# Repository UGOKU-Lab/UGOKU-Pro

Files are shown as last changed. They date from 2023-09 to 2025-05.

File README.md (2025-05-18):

# UGOKU One
UGOKU Pro のハードウェア設計データ（KiCADデータ）のリポジトリです。

UGOKU Pro はモータやセンサを使ったロボットなどのアプリケーションを少しでも手軽にテスト、制御することを目的に開発している汎用基板です。

広く普及しているマイコンボードや無線モジュールに加え、高出力なDCモータドライバを2個搭載しています。さらに、汎用IOポートを設け幅広いアプリケーションに対応します。
Androidアプリ[FlexConsole](https://github.com/UGOKU-Lab/FlexConsole_for_Bluetooth_Serial)と組み合わせることでスマートフォンから手軽に遠隔操作や監視が行えます。

[](

)

| 主要搭載部品 |  |
----|---- 
| マイコンボード | Nucleo-F303K8 | 
| 無線モジュール | ESP32-WROOM-32E |
| DCモータドライバ | 2× TB67H303HG |
| CANトランシーバ | MCP2562-E/SN |

# 使用ライブラリ
[SnapMagic](https://www.snapeda.com/home/) よりダウンロードしたKiCADのライブラリ（CC BY-SA）を使用しています

# ライセンス
<br />この データ は <a rel="license" href="http://creativecommons.org/licenses/by-sa/4.0/deed.ja">クリエイティブ・コモンズ 表示 4.0 国際 ライセンス</a>の下に提供されています。

本データおよび本データにより製作した基板は良識の範囲で自由に非営利、営利問わず使用できます。また、改変、再配布も可能です。
ただし、再配布の際には本リポジトリのリンクを掲載を希望します。（本プロジェクトの目的に即した改良についてはプルリクエストを歓迎します）。  
また、本データにより生じた損害等の一切の責任を負いかねますので、ご了承ください。

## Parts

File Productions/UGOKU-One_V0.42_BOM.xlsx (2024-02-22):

Comment | Designator | Footprint | JLCPCB Part #（optional）
100nF | C1, C11, C13, C2, C3, C4, C9 | C0805 | C1711
3.3uF | C10 | C0805 | C2182175
51k | R13, R7 | R0603
10k | R2, R3, R12, R9 | R0603
120 | R1 | R0603
510 | R4 | R0603 | C965132
1k | R5, R6 | R0603
LED | L1 | L0805 | C264427
LED | L2, L3 | L0805 | C86865
Diode | D1 | SOD-123F
SSSS213202 | SW3, SW5 |  | C115375
TL3301FF160QG | SW1, SW2 |  | C273522
SKRPABE010 | SW4 |  | C115360
MCP2562-E/SN | U6 | SOIC127P600X175-8N | C53609
ESP32-WROOM-32E-N16 | U7 |  | C701343
TB67H303HG | U4,U5 |  | C1556864
1792863 | T1,T2,T3 |  | C3032345
A2541WV-3P | J4 |  | C5333416
B03B-XASK-1-A(LF)(SN) | CN4 |  | C264992
B04B-XASK-1(LF)(SN) | CN1,CN2,CN3 |  | C264994
A2541HWV-4P | J6 |  | C5176037
PZ254V-12-6P | J1 |  | C492420
B-2200S15P-A120 | P1,P2 |  | C124408

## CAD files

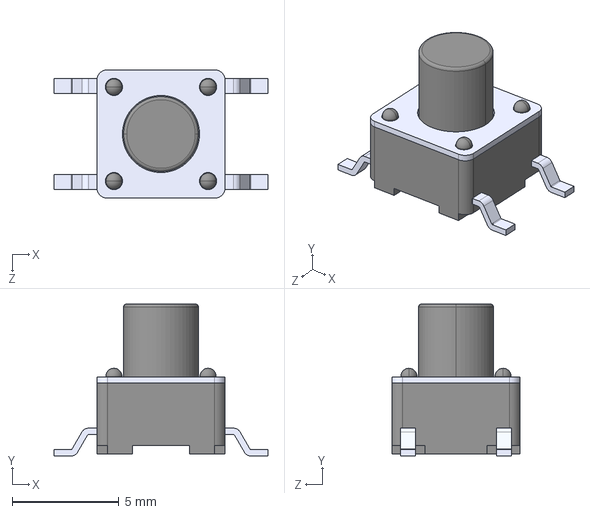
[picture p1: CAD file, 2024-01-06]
3Dmodels/TL3301FF160QG.step
10.0 x 7.10 x 6.00 mm

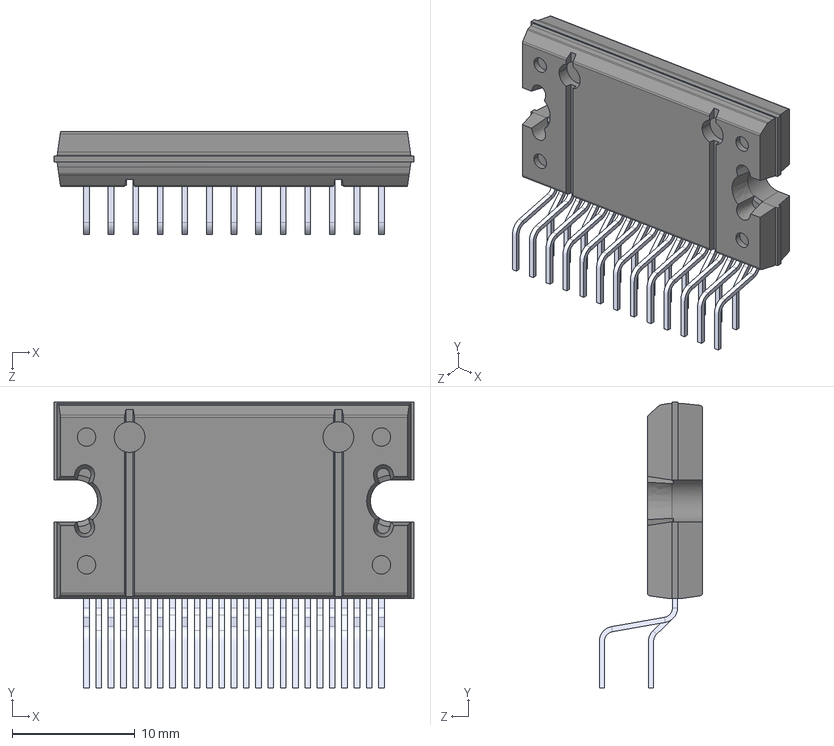
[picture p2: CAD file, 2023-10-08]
3Dmodels/TB67H303HG.step
29.3 x 23.3 x 8.41 mm

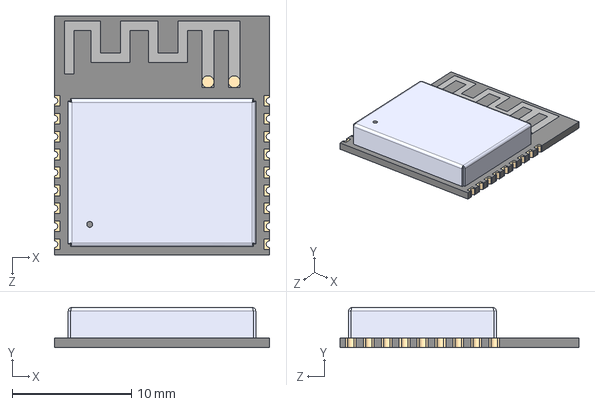
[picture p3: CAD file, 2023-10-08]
3Dmodels/ESP32-C3-WROOM-02-N4.step
18.0 x 3.35 x 20.0 mm

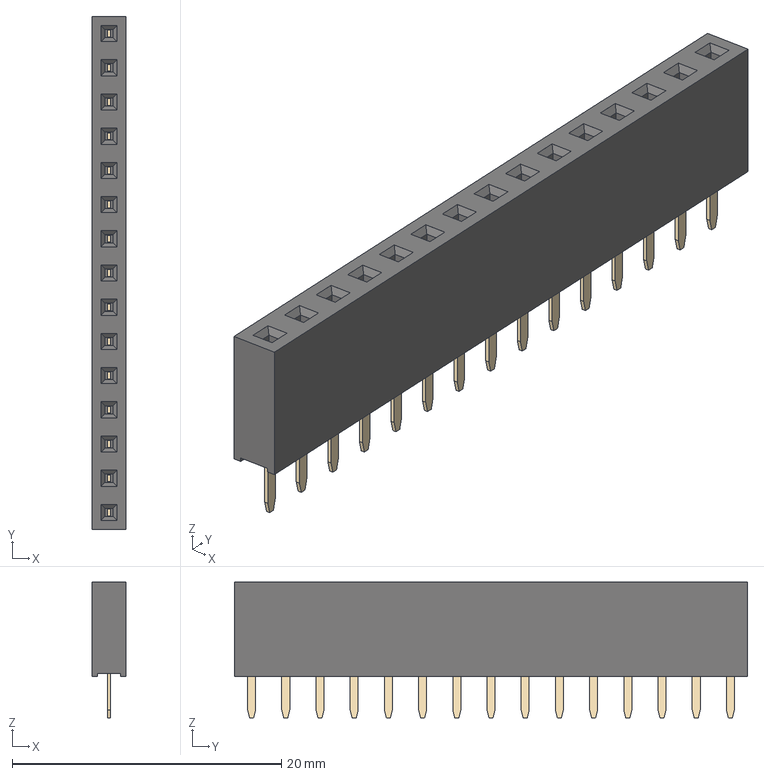
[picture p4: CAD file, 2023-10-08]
3Dmodels/PinSocket_1x15_P2.54mm_Vertical.step
2.54 x 38.1 x 10.1 mm

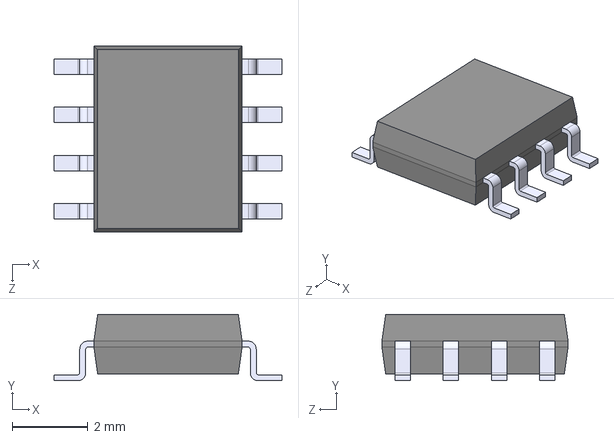
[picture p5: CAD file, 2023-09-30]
3Dmodels/MCP2562-E_SN.step
6.00 x 1.75 x 4.90 mm

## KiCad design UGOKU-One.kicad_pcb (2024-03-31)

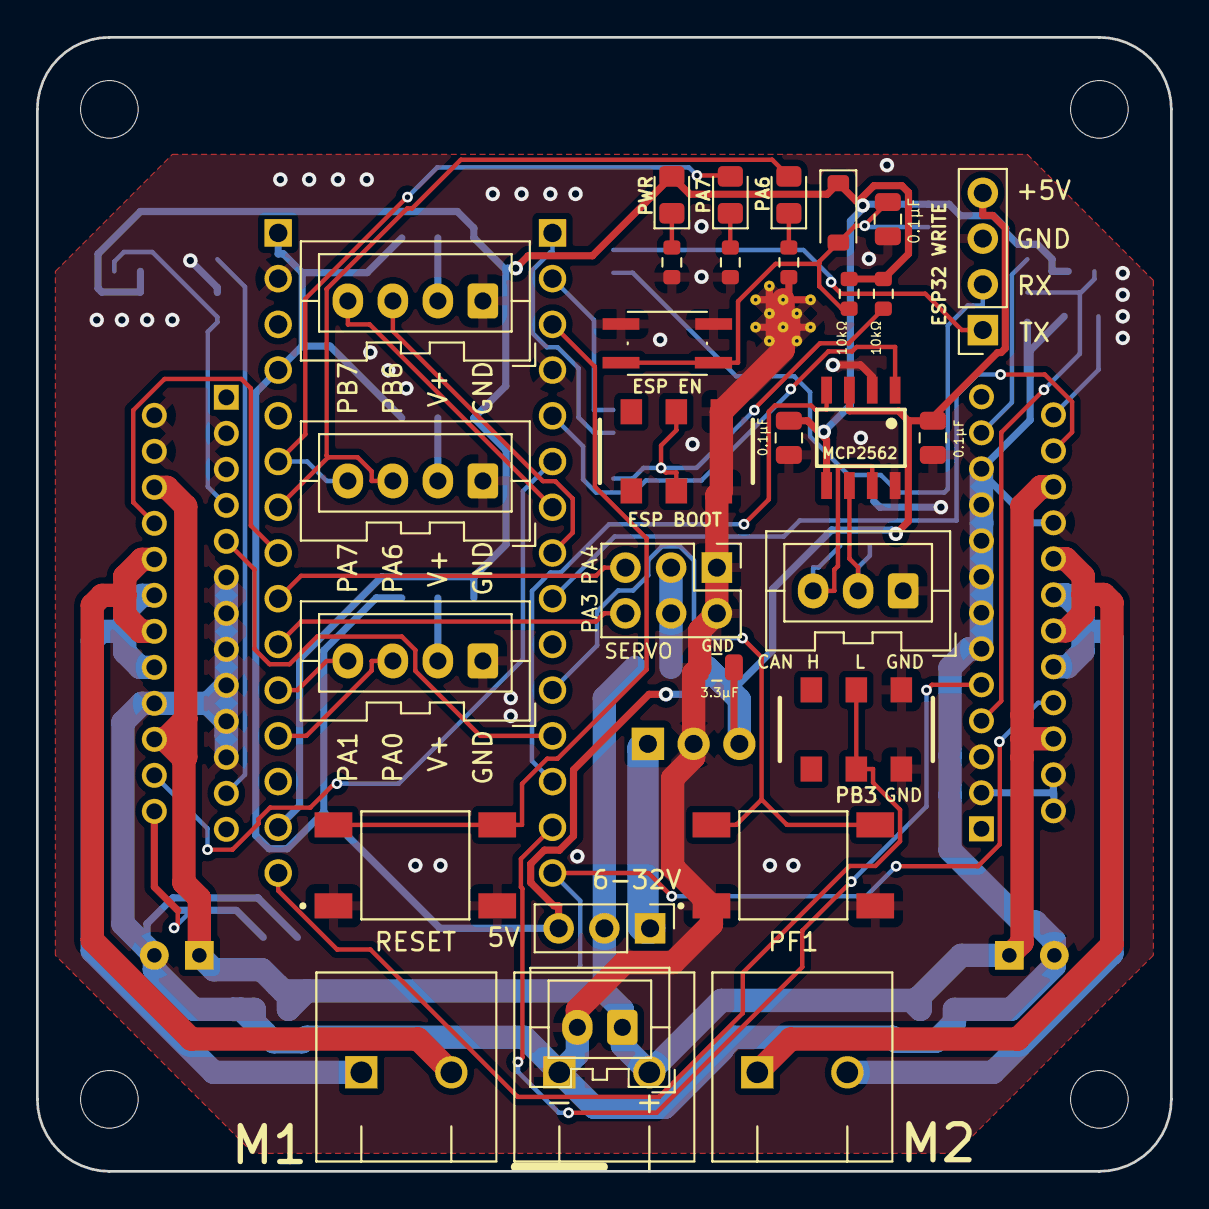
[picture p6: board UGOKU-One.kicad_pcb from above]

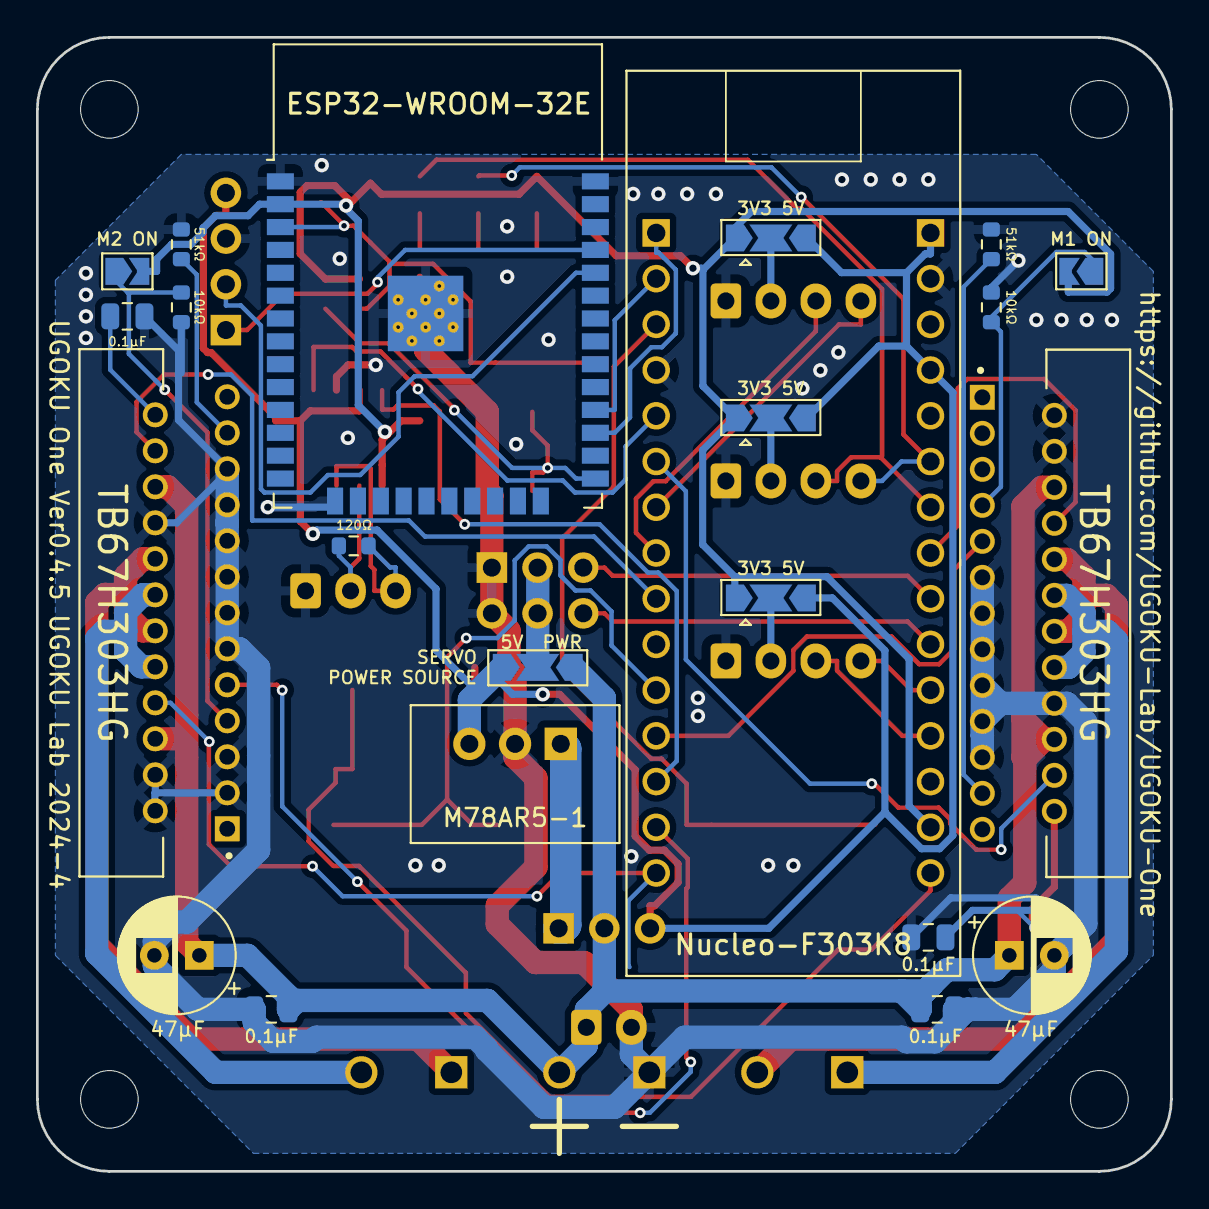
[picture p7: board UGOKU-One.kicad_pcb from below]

Board: 2 copper layers, 63.0 x 63.0 mm, 56 parts (22 on the bottom side), 49 nets.

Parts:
C1, C2, C3, C4, C9, C11, C13: 0.1μF; C_0805_2012Metric
C5, C12: 47μF; CP_Radial_D6.3mm_P2.50mm
C10: 3.3μF; C_0805_2012Metric
CN1, CN2, CN3: Conn_01x04; JST_XA_B04B-XASK-1_1x04_P2.50mm_Vertical
CN4: CAN; JST_XA_B03B-XASK-1_1x03_P2.50mm_Vertical
D1: D; D_SOD-123
J2: Conn_02x03_Odd_Even; PinHeader_2x03_P2.54mm_Vertical
J3: Conn_01x02_Male; JST_XA_B02B-XASK-1_1x02_P2.50mm_Vertical
J4: PA10; PinHeader_1x03_P2.54mm_Vertical
J6: Conn_01x04; PinSocket_1x04_P2.54mm_Vertical
JP1, JP2, JP3, JP4: Jumper_NC_Dual; SolderJumper-3_P2.0mm_Open_TrianglePad1.0x1.5mm
L1: PWR; LED_0805_2012Metric_Pad1.15x1.40mm_HandSolder
L2, L3: LED; LED_0805_2012Metric_Pad1.15x1.40mm_HandSolder
MH1, MH2, MH3, MH4: MountingHole_3.2mm_M3
MJP1, MJP2: Jumper; SolderJumper-2_P1.3mm_Open_TrianglePad1.0x1.5mm
R1: 120Ω; R_0603_1608Metric
R2, R3: 10kΩ; R_0603_1608Metric
R4, R5, R6: 3.3k; R_0603_1608Metric
R7, R13: 51kΩ; R_0603_1608Metric
R9, R12: 10k; R_0603_1608Metric
SW1: PF1; SW_TL3301FF160QG
SW2: RESET; SW_TL3301FF160QG
SW3, SW5: SW_Push_DPDT; SSSS213202
SW4: SW_Push_1P1T_NO_Vertical_Wuerth_434133025816
T1, T2, T3: PTS_1.5_2
U1: M78AR5-1; M78AR
U2: NUCLEO-F303K8; MODULE_NUCLEO-F303K8
U4, U5: TB67H303HG; TO100P2930X465X1937-25
U6: MCP2562-E_SN; SOIC127P600X175-8N
U7: ESP32-WROOM-32

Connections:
+3V3: C2.1, D1.1 (K), JP1.1, JP2.1, JP3.1, L1.2 (A), MJP1.2, MJP2.2, R9.2, R12.2, U2.4_14 (+3V3), U6.5 (VIO), U7.2 (VDD)
+5V: C1.1, C10.1, J4.3, J6.4, JP1.3, JP2.3, JP3.3, JP4.3, U1.3 (Vout), U2.4_1 (VIN), U2.4_4 (+5V), U6.3 (VDD)
GND: C1.2, C2.2, C3.2, C4.2, C5.2, C9.2, C10.2, C11.2, C12.2, C13.2, CN1.1, CN2.1, CN3.1, CN4.1, J2.1, J2.2, J3.2, J6.3, R2.1, R3.1, R4.1, R5.1, R6.1, R7.2, R13.2, SW1.1, SW2.1, SW3.3 (C), SW3.6 (C), SW4.1, SW5.3 (C), SW5.6 (C), T3.P$1, U1.2 (GND), U2.3_4 (GND_1), U2.4_2 (GND_2), U4.2 (SGND), U4.3 (SELECT), U4.4 (TEST1), U4.5 (VREF), U4.11 (RSB), U4.13 (PGNDB), U4.15 (RSA), U4.17 (PGNDA), U4.18 (TEST2), U4.19 (TEST3), U4.21 (TEST4), U5.2 (SGND), U5.3 (SELECT), U5.4 (TEST1), U5.5 (VREF), U5.11 (RSB), U5.13 (PGNDB), U5.15 (RSA), U5.17 (PGNDA), U5.18 (TEST2), U5.19 (TEST3), U5.21 (TEST4), U6.2 (VSS), U6.8 (STBY), U7.1 (GND), U7.15 (GND), U7.38 (GND), U7.39 (GND)
unnamed: CN1.2, JP3.2
unnamed: CN1.3, U2.3_8 (PB6)
unnamed: CN1.4, U2.3_7 (PB7)
unnamed: CN2.2, JP2.2
unnamed: CN2.3, L3.2 (A), U2.4_7 (PA6)
unnamed: CN2.4, L2.2 (A), U2.4_6 (PA7)
unnamed: CN3.2, JP1.2
unnamed: CN3.3, U2.4_12 (PA0)
unnamed: CN3.4, U2.4_11 (PA1)
unnamed: CN4.2, R1.1, U6.6 (CANL)
unnamed: CN4.3, R1.2, U6.7 (CANH)
unnamed: C9.1, D1.2 (A), R9.1, SW4.2, U7.3 (EN)
unnamed: J2.3, J2.4, JP4.2
unnamed: J2.5, U2.4_9 (PA4)
unnamed: J2.6, U2.4_10 (PA3)
unnamed: J4.1, U1.1 (Vin)
unnamed: J6.1, U7.35 (TXD0/IO1)
unnamed: J6.2, U7.34 (RXD0/IO3)
unnamed: L1.1 (K), R4.2
unnamed: L2.1 (K), R5.2
unnamed: L3.1 (K), R6.2
unnamed: SW2.2, U2.3_3 (NRST_1)
unnamed: U2.3_12 (PA8), U5.9 (IN2)
unnamed: U2.3_1 (PA9), U7.27 (IO16)
unnamed: U2.3_2 (PA10), U7.28 (IO17)
unnamed: U2.3_13 (PA11), U6.4 (RXD)
unnamed: U2.3_5 (PA12), U6.1 (TXD)
unnamed: U2.3_6 (PB0), U5.22 (PWM)
unnamed: U2.3_9 (PB1), U4.22 (PWM)
unnamed: U2.3_15 (PB4), U4.8 (IN1)
unnamed: U2.3_14 (PB5), U4.9 (IN2)
unnamed: SW1.2, U2.3_11 (PF1)
unnamed: U2.4_8 (PA5), U5.8 (IN1)
unnamed: SW5.2 (B), SW5.5 (B), U2.4_15 (PB3)
unnamed: R13.1, U4.23 (OSC)
unnamed: T2.P$1, U4.12 (OUT1B), U4.16 (OUT1A)
unnamed: T2.P$2, U4.10 (OUT2B), U4.14 (OUT2A)
unnamed: MJP1.1, R2.2, U4.7 (STBY)
unnamed: C13.1, U4.24 (VREG)
unnamed: R7.1, U5.23 (OSC)
unnamed: T1.P$1, U5.12 (OUT1B), U5.16 (OUT1A)
unnamed: T1.P$2, U5.10 (OUT2B), U5.14 (OUT2A)
unnamed: MJP2.1, R3.2, U5.7 (STBY)
unnamed: C3.1, U5.24 (VREG)
unnamed: R12.1, SW3.2 (B), SW3.5 (B), U7.25 (IO0)
PWR: C4.1, C5.1, C11.1, C12.1, J3.1, J4.2, JP4.1, T3.P$2, U4.6 (VCC), U4.20 (VCC), U5.6 (VCC), U5.20 (VCC)

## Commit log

2023-09-30 Add files via upload
    initial commit
    [MultiBoardMini.kicad_pcb, MultiBoardMini.kicad_sch]
2023-10-01 回路図にESP32モジュール追加
    [MultiBoardMini.kicad_sch]
2023-10-02 ESP32モジュールのライブラリを追加
2023-10-08 change Libraries path, update design
    [MultiBoardMini.kicad_pcb, MultiBoardMini.kicad_sch]
2023-10-08 update Library path setting, design
    [ESP32-C3-WROOM-02-N4.step, MCP2562-E_SN.step, MultiBoardMini_HW.kicad_pcb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]
2023-10-21 update sch
    [MultiBoardMini_HW.kicad_sch]
2023-10-22 add slide switch footprints
    [MultiBoardMini_HW.kicad_pcb, MultiBoardMini_HW.kicad_sch]
2023-10-22 ERC実行に伴うエラーの解消 ・CANコネクタの接続ができていなかったので接続した。 ・モータドライバのライブラリのIO特性が設定されていないせいでエラーが出ていたが、問題ないとして除外項目に追加した。
    [MultiBoardMini_HW.kicad_sch]
2023-10-22 Update iroiro
    [MultiBoardMini_HW.kicad_pcb, MultiBoardMini_HW.kicad_sch]
2023-10-22 部品は一おおむね完了
    [MultiBoardMini_HW.kicad_pcb, MultiBoardMini_HW.kicad_sch]
2023-10-22 PWR MOT 配線一旦できた
    [MultiBoardMini_HW.kicad_pcb, MultiBoardMini_HW.kicad_sch]
2023-10-22 MOT PWR 修正
    [MultiBoardMini_HW.kicad_pcb]
2023-10-22 自動配線前のいろいろごにょごにょしたやつ
    [MultiBoardMini_HW.kicad_pcb]
2023-10-22 オートルート前のほぼ完成
    [MultiBoardMini_HW.kicad_pcb]
2023-10-22 Autoroute 前の完成だと思われるもの
    [MultiBoardMini_HW.kicad_pcb]
2023-10-22 配線一応できた
    [MultiBoardMini_HW.kicad_pcb]
2023-10-22 配線一応完了 DRC確認済み
    [MultiBoardMini_HW.kicad_pcb]
2023-10-22 ほぼ完成みたいなもの
    [MultiBoardMini_HW.kicad_pcb]
2023-10-24 緊急発注用
    [MultiBoardMini_HW.kicad_pcb, MultiBoardMini_HW.kicad_sch]
2023-11-11 改良版の電源配線暫定版
    [MultiBoardMini_HW.kicad_pcb, MultiBoardMini_HW.kicad_sch]
2023-11-11 ESP大型化のためつめつめ
    [MultiBoardMini_HW.kicad_pcb]
2023-11-12 esp32変更
    [MultiBoardMini_HW.kicad_sch]
2023-11-23 回路図 ESP32の回路修正完了
    [MultiBoardMini_HW.kicad_sch]
2023-11-25 手動配線完成
    [MultiBoardMini_HW.kicad_pcb]
2023-11-25 MOT配線見直し
    [MultiBoardMini_HW.kicad_pcb]
2023-11-25 MDGND配線見直し
    [MultiBoardMini_HW.kicad_pcb]
2023-11-25 配線完成
    [MultiBoardMini_HW.kicad_pcb, MultiBoardMini_HW.kicad_sch]
2023-11-25 ほぼ完成
    [MultiBoardMini_HW.kicad_pcb]
2023-11-26 V0.41試作発注用完成 PCB ASSEMBLY用BOM、positionデータ追加
    [MBM_V0.41_BOM.xlsx, MBM_V0.41_positions.csv, MultiBoardMini_HW.kicad_pcb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]
2023-11-26 とりあえず保存
    [MultiBoardMini_HW.kicad_sch]
2024-01-03 GNDと5V+がつながっていた問題を解消
    [MultiBoardMini_HW.kicad_pcb, MultiBoardMini_HW.kicad_sch]
2024-01-05 回路図変更
    [MultiBoardMini_HW.kicad_sch]
2024-01-05 ESPとNucleoが接続されてなかったので接続
    [MBM_V0.41_BOM.xlsx, MBM_V0.41_positions.csv, MultiBoardMini_HW.kicad_pcb]
2024-01-06 Change Project name
    [MBM_V0.41_BOM.xlsx, MBM_V0.41_positions.csv, MultiBoardMini_HW.kicad_pcb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]
2024-01-06 Change name 再び
    [UGOKU-One_HW.kicad_pcb, UGOKU-One_HW.kicad_sch]
2024-01-07 2024/1/6発注仕様
    [UGOKU-One.kicad_pcb, UGOKU-One_V0.42_BOM.xlsx, UGOKU-One_V0.42_positions.csv]
2024-01-21 Via size modified to match JLCPCB rules
    [UGOKU-One.kicad_pcb, UGOKU-One.kicad_sch]
2024-01-29 Motor driver STM pin assignment replacement
    [UGOKU-One.kicad_pcb, UGOKU-One.kicad_sch, UGOKU-One_V0.42_BOM.xlsx]
2024-01-29 Motor driver STM pin assignment replacement completed
    [UGOKU-One.kicad_pcb, UGOKU-One.kicad_sch]
2024-02-10 update silk version
    [UGOKU-One.kicad_pcb]
2024-02-22 Update Diode footprint and servo pin header
    [UGOKU-One.kicad_pcb, UGOKU-One.kicad_sch, UGOKU-One_V0.42_BOM.xlsx]
2024-03-01 XA使用Verの最終版
    [UGOKU-One.kicad_pcb, UGOKU-One.kicad_sch]
2024-03-03 V0.4.4 2024-3-3 発注仕様
    [UGOKU-One.kicad_pcb, UGOKU-One_V0.4.4_BOM.xlsx, UGOKU-One_V0.4.4_positions.csv]
2024-03-15 saisinban(XA仕様)
    [UGOKU-One.kicad_sch, UGOKU-One_V0.4.4_BOM.xlsx]
2024-03-31 Modify ESP32 position
    [UGOKU-One.kicad_pcb, UGOKU-One_V0.4.4_BOM.xlsx]

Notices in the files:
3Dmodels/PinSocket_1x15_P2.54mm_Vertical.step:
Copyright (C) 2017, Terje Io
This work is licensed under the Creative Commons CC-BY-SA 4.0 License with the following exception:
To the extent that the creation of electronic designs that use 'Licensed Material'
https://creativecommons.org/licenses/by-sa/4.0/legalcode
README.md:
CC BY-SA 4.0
